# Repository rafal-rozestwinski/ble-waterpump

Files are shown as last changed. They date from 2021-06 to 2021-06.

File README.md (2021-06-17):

# Bluetooth Low Energy IoT Water Pump powered by AA batteries

Another item in my home IoT system, a AA-battery powered pump for watering plants controlled over Bluetooth Low Energy (BLE).

# Design - cheap, fast, reliable vs quick 'n dirty

- Chip nrf51822 is **old and obsolete**, included firmware **(softdevice) is buggy**. But it's **cheap ($1)** and **available** in bulk. When using nrf52* series, I recommend using either native nordic semi SDK or [mbed examples](https://github.com/ARMmbed/mbed-os-example-ble).
- It's an **amazing device for radio controlled battery operated IoT devices**. In this project, it's directly **powered from a two AA batteries**, with **power consumption of around 1.5mA**. Therefore it should work for more than **2 months on a single charge**.
- Three AA batteries power the 5V cheap ($1) watertight water pump. A separate power source for pump here is being used to simplify project and avoid inefficient regulators. Pump, when running, is consuming between 70 and 100mA. [NPM BC547](https://www.mouser.com/datasheet/2/149/BC547-190204.pdf) is rated for 100mA continuous.
- uC battery level is measured and available over BLE GATT service. I changed that to use internal reference voltage, not implemented in mBed.
- **3xAA battery level is not measured**. I check those from time to time, as pump runs for just a few seconds every day.
- Project is downloaded from ARM mbed online IDE and adjust to **work in an offline mode**, using normal GCC ARM build on ubuntu etc.
- No encryption nor secure pairing.
- *WDT is enabled*, but in addition device reboots every 1024 seconds, as a additional failsafe for unstable (old) SoftDevice.
- Just a *few passive components* and a *single [BJT NPM](https://www.mouser.com/datasheet/2/149/BC547-190204.pdf)* transistor being used.
- Code is forked from some mbed example in a quite dirty way. **No warranty** ;)

# Building

- Install ARM GCC on ubuntu: `sudo apt install gcc-arm-none-eabi gdb valgrind make openocd srecord`
- Connect STLINK programmer to SWDIO/SWCLK/GND/VCC pins (with batteries disconnected) and attach to the computer.
- `make && ./RR_FLASH.sh`
- Check using `gatttool` on linux/RPI or via official [nRF Connect app](https://apps.apple.com/app/nrf-connect-for-mobile/id1054362403), which is very useful for debugging BLE in general. 
- Use my python tool `pumpble.py`, available in this directory (including `requirements.txt`).

# Electronic Connection Diagram

As my cheap imported [nrf51822](https://www.nordicsemi.com/Products/Low-power-short-range-wireless/nRF51822) [cheap module](https://botland.com.pl/moduly-bluetooth/4505-modul-bluetooth-low-energy-ble-40-nrf51822-waveshare-9515.html) has 2.0mm goldpin spacing, I'm using [wire-wrapping](https://en.wikipedia.org/wiki/Wire_wrap) technique to connect it.

```
[ 3xAA battery + ] ---------+------[+ 5V water pump -]-----+--------+
                            |                              |        |
                            +------[   |< diode   ]--------+        |  
                                                                 | /
                                          +--[  360 Ohm  ]-----  |   NPN BJT BC547
                                          |                      | \>
                                          |                         |
                                        PIN19                       |
                               ==========================           |
                               |                        |           |
                               |   nrf51822 module      |+-------- Common GND
                     +--VCC +--|                        |           |
                     |         ===========================          |
                     |                       PIN2                   |
                     |                        |                     |
                     |                        |                     |
[ 2*AA battery + ] --+---- [  6800 Ohm  ] ----+---- [ 680 Ohm ] ----+
```

Note: PIN18 is a blinking status LED. Not attached to save battery.

# Hardware

STL and FreeCAD files for attaching pump to the 5mm silicone tube, as well as compatible splitter (so single pump can serve multiple pots etc.). Those are in CAD/ directory.

# Usage [Linux/raspberry pi]

### Find device MAC:

Run `hcitool lescan` and lookup for a device name configured in `main.cpp` as `DEVICE_NAME[]`.

```bash
$ sudo hcitool lescan | grep -i waterpump
C8:5E:22:9A:21:3A waterpump
```

### Find handle values:

```bash
$ gatttool -t random -b C8:5E:22:9A:21:3A --characteristics
(...)
handle = 0x000d, char properties = 0x12, char value handle = 0x000e, uuid = 0000a301-0000-1000-8000-00805f9b34fb
handle = 0x0011, char properties = 0x0a, char value handle = 0x0012, uuid = 0000a101-0000-1000-8000-00805f9b34fb
handle = 0x0014, char properties = 0x02, char value handle = 0x0015, uuid = 0000a201-0000-1000-8000-00805f9b34fb
```

Where first part of UUIDs define services:

- 0000a101-0000-1000-8000-00805f9b34fb -> 0xA101 - pump characteristic uuid for reading and writing a value
- 0000a201-0000-1000-8000-00805f9b34fb -> 0xA201 - uptime characteristic uuid for reading a value
- 0000a301-0000-1000-8000-00805f9b34fb -> 0xA301 - battery characteristic for reading a value

Use `char value handle` value when calling commands below for particular service.

### Read battery state

Value returned is hex-encoded byte, where for example value of 64 => 0x64 => 100 => 100%

`gatttool -t random  -b $MAC --char-read --handle=0x0e | cut -d':' -f2`

### Read uptime

Returns 4 bytes, uint32_t of uptime in seconds since last reboot:

`gatttool -t random  -b $MAC --char-read --handle=0x15 | cut -d':' -f2`

### Read pump state (pumping or not)

`gatttool -t random  -b $MAC --char-read --handle=0x12 | cut -d':' -f2`

### Start pump

Value = seconds for which it should be running, as an hex-encoded byte (and padded with 0!):

`gatttool -t random  -b $MAC --char-write-req -a 0x0012 -n 05`

### Wrapper tool

`LINUX_BLE_GATTTOOL_TEST.sh` is my wrapper to perform those steps. I run it over ssh over my all raspberry pi's all over my home, which is integrated with custom `sensors-dashboard` as well as with the (http://homebridge.io)[HomeBridge] for iOS/HomeKit integration. One can also use iOS Shortcuts app to perform the same.

# Media

Note: always use properly matched batteries ;)

Note: due to a lot of hot glue being used, my implementation has scored only 6/10 repairability score ;)

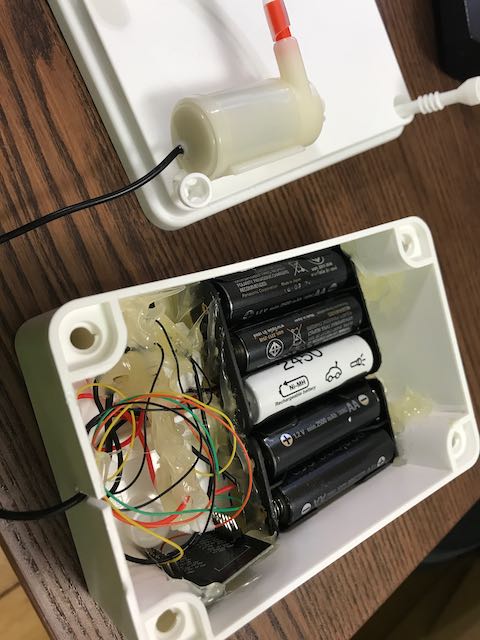
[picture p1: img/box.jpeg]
Photo - inside the box Battery box

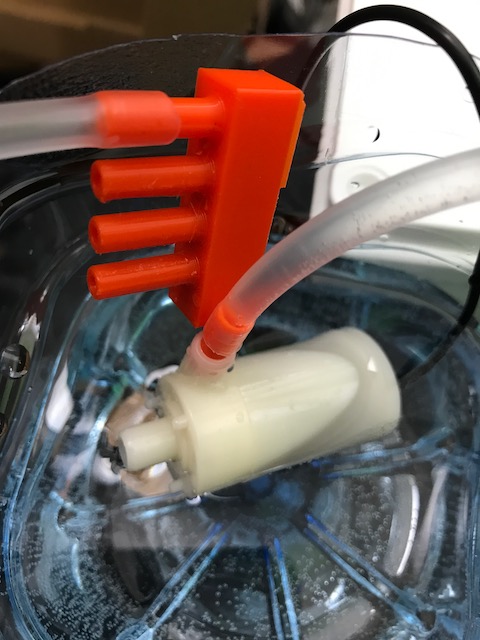
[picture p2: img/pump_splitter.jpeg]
Photo - physical water splitter 3D printed water splitter

Video - pumping water Pumping in action
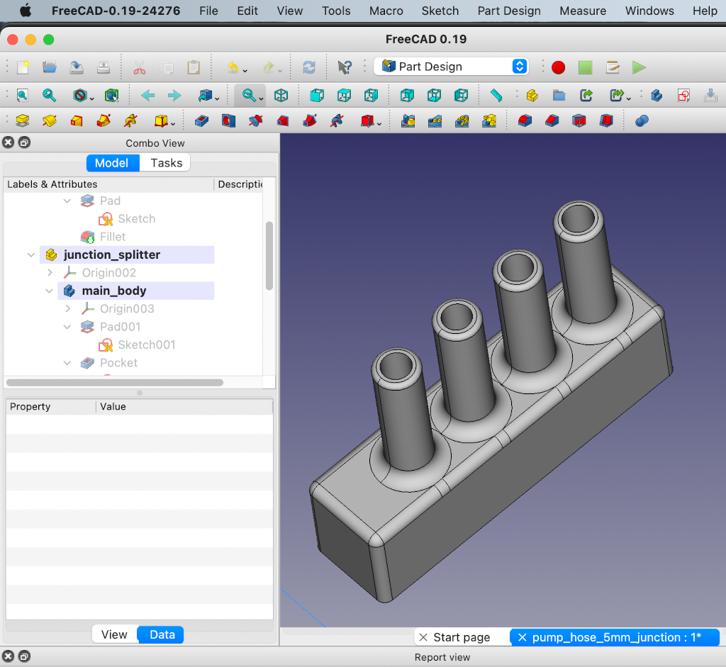
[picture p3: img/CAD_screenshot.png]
FreeCAD - water splitter FreeCAD screenshot of water splitter


# Learn more about GATT and BLE

- https://epxx.co/artigos/bluetooth_gatt.html

# Licensing

All-but-some files in this repo were exported/downloaded from [ARM's mBed Studio online](https://os.mbed.com/studio/).

My changes? Choose: Apache 2, MIT, BSD.

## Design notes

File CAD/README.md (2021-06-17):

# CAD files - STL and FreeCAD

Photo - physical water splitter 3D printed water splitter
FreeCAD - water splitter FreeCAD screenshot of water splitter

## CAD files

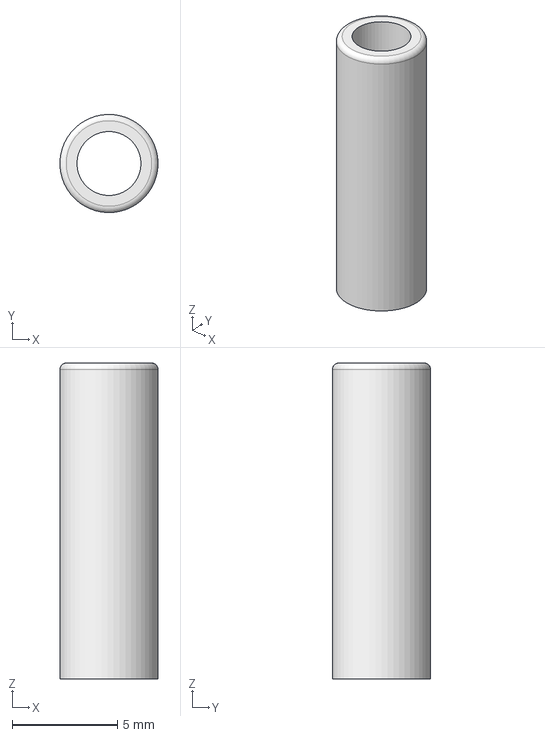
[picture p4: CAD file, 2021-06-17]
CAD/pump_hose_5mm_adapter.FCStd
4.66 x 4.66 x 15.0 mm

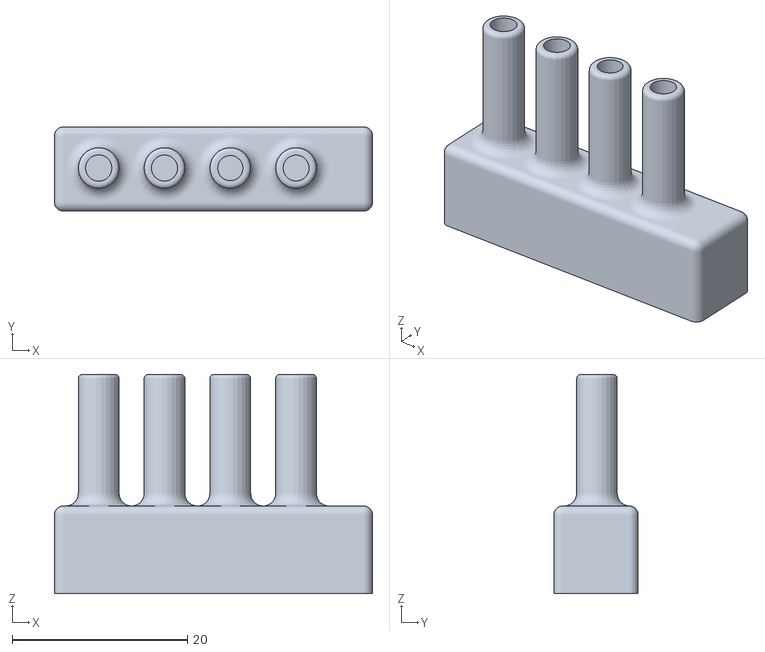
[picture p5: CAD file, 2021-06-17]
CAD/pump_hose_5mm_junction-junction_splitter.stl
36.2 x 9.60 x 25.0

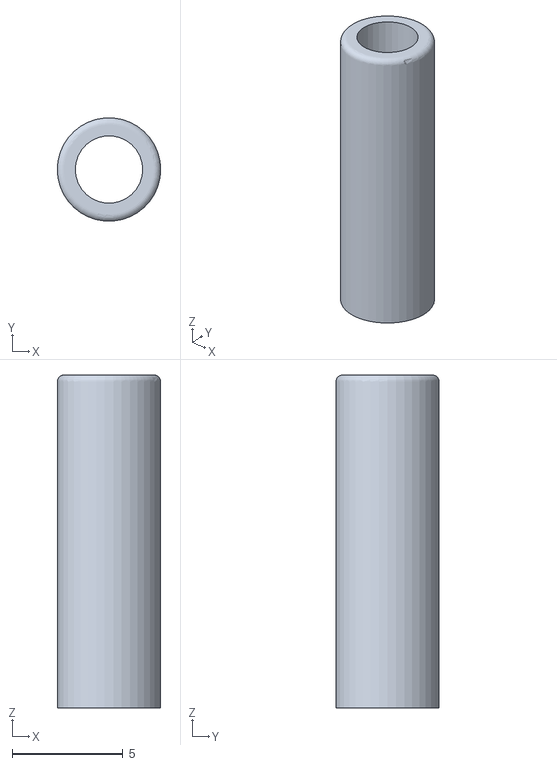
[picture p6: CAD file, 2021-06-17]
CAD/pump_hose_5mm_adapter-Body.stl
4.66 x 4.64 x 15.0

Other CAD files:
CAD/pump_hose_5mm_junction.FCStd

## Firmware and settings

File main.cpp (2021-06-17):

// nrf51822 BLE water pump powered by AA batteries
// by Rafal Rozestwinski
// Modified nrf mbed example.
// My changes under any of: Apache 2.0, BSD, MIT.

#ifndef DEV_NAME
#define DEV_NAME waterpump
#endif

#ifndef DISCONNECT_AFTER_SECONDS
#define DISCONNECT_AFTER_SECONDS 10
#endif

#ifndef RESET_AFTER_SECONDS
#define RESET_AFTER_SECONDS 3600
#endif



#define STRINGIZE(x) #x
#define STRINGIZE_VALUE_OF(x) STRINGIZE(x)

// BATTERY LEVEL:  VCC - R1 - ADC - R2 - GND
// with those values (6.8k + 680R): 12V = 1.09V; 3V = 0.273V; 5V = 0.455
// around 9% of actual value.
#define R1 6800
#define R2 680
#define REFERENCE_VOLTAGE 1.2f

#include <inttypes.h>
#include "ble/BLE.h"
#include "mbed.h"
#include "ble/services/BatteryService.h"
#include "ble/services/DeviceInformationService.h"
#include "nrf.h" // watchdog
#include "cmsis.h"
#include "pinmap.h"

// via ./mbed/TARGET_NRF51822/TOOLCHAIN_GCC_ARM/PinNames.h
//    LED1    = p18,
//    LED2    = p19,
//    LED3    = p20,
//    LED4    = p19,
//    BUTTON1 = p16,
//    BUTTON2 = p17,
//    //  RX_PIN_NUMBER = p11,  TX_PIN_NUMBER = p9,
//    USBTX = TX_PIN_NUMBER,
//    USBRX = RX_PIN_NUMBER,
// DEFAULT: sudo miniterm /dev/ttyUSB0 9600
// HERE: sudo miniterm /dev/ttyUSB0 115200
// Battery voltage with R1 and R2: p2

#define RR_ANALOGIN_MEDIAN_FILTER      1
#define RR_ADC_10BIT_RANGE             0x3FF
#define RR_ADC_RANGE    RR_ADC_10BIT_RANGE

void p2_adc_configure_internal_1_2V_ref() {
    NRF_ADC->ENABLE = ADC_ENABLE_ENABLE_Enabled;
    NRF_ADC->CONFIG = (ADC_CONFIG_RES_10bit << ADC_CONFIG_RES_Pos) |
//                      (ADC_CONFIG_INPSEL_AnalogInputOneThirdPrescaling << ADC_CONFIG_INPSEL_Pos) |
//                      (ADC_CONFIG_REFSEL_VBG << ADC_CONFIG_REFSEL_Pos) |
//                      (ADC_CONFIG_REFSEL_SupplyOneThirdPrescaling << ADC_CONFIG_REFSEL_Pos) | // NRF_ADC_CONFIG_REF_VBG
                      (ADC_CONFIG_PSEL_AnalogInput3 << ADC_CONFIG_PSEL_Pos);// |
//                      (ADC_CONFIG_EXTREFSEL_None << ADC_CONFIG_EXTREFSEL_Pos);
}

uint16_t p2_adc_read_u16() {
    NRF_ADC->CONFIG     &= ~ADC_CONFIG_PSEL_Msk;
    NRF_ADC->CONFIG     |= ADC_CONFIG_PSEL_AnalogInput3 << ADC_CONFIG_PSEL_Pos;
    NRF_ADC->TASKS_START = 1;
    while (((NRF_ADC->BUSY & ADC_BUSY_BUSY_Msk) >> ADC_BUSY_BUSY_Pos) == ADC_BUSY_BUSY_Busy) {
    }
    return (uint16_t)NRF_ADC->RESULT; // 10 bit
}

float p2_adc_read() {
    uint16_t value = p2_adc_read_u16();
    return (float)value * (1.0f / (float)RR_ADC_RANGE);
}

void wdt_init() {
    NRF_WDT->CONFIG = (WDT_CONFIG_HALT_Pause << WDT_CONFIG_HALT_Pos) | ( WDT_CONFIG_SLEEP_Run << WDT_CONFIG_SLEEP_Pos);
    NRF_WDT->CRV = 3*32768;
    NRF_WDT->RREN |= WDT_RREN_RR0_Msk;
    NRF_WDT->TASKS_START = 1;
}

void wdt_reset() {
    NRF_WDT->RR[0] = WDT_RR_RR_Reload;
}

DigitalOut led1(LED1);
DigitalOut powerswitch1(LED2);

Serial serial(USBTX, USBRX, 115200);
Ticker ticker;
volatile uint32_t cnt = 0;

void rr_reset() {
    NVIC_SystemReset();
}

void periodicCallback(void);
const char* get_current_sensor_name(int b1, int b2);

void rr_error() {
    serial.printf("> rr_error() - 1s loop for debugger now!\n");
    ticker.detach();
    ticker.attach(periodicCallback, 0.1);
    wait_ms(1000);
    rr_reset();
}

float nrf51_voltage_adc_to_battery(float adc_in) {
    float real_voltage_on_pin = adc_in * REFERENCE_VOLTAGE;
    //int R1 = 21000; // defined as macro
    //int R2 = 1000; //  defined as macro
    //   Vs ----- R1 ------ Vout_PIN ---- R2 ----- GND
    //
    //         Vs * R2
    // Vout = ---------------
    //        ( R1 + R2)
    //
    //          Vout
    // Vs =   -------- * ( R1 + R2)
    //          R2
    float actualVoltage = (real_voltage_on_pin / R2) * (R1 + R2);
    return actualVoltage;
}

int32_t map(int32_t x, int32_t in_min, int32_t in_max, int32_t out_min, int32_t out_max) {
    int32_t ret = (x - in_min) * (out_max - out_min) / (in_max - in_min) + out_min;
    if(ret > out_max) return out_max;
    if(ret < out_min) return out_min;
    return ret;
}

float LAST_BATTERY_VOLTAGE = 0.0f;
uint8_t LAST_BATTERY_PERCENT = 0;

float get_current_battery_voltage() {
    float adc_out = p2_adc_read(); // using internal 1.2V reference voltage, same below.
    float voltage = nrf51_voltage_adc_to_battery(adc_out);
    return voltage;
}

void periodicCallback(void) {
    led1 = !led1;
    cnt++;
}

class WaterPumpService {
public:
    const static uint16_t WATER_PUMP_SERVICE_UUID              = 0xA100;
    const static uint16_t WATER_PUMP_STATE_CHARACTERISTIC_UUID = 0xA101;

    WaterPumpService(BLEDevice &_ble, uint8_t initial) :
        ble(_ble), pumpingValue(initial), pumpState(WATER_PUMP_STATE_CHARACTERISTIC_UUID, &initial) {
        GattCharacteristic *charTable[] = {&pumpState};
        GattService pumpService(WATER_PUMP_SERVICE_UUID, charTable, sizeof(charTable) / sizeof(GattCharacteristic *));
        ble.addService(pumpService);
    }

    GattAttribute::Handle_t getValueHandle() const {
        return pumpState.getValueHandle();
    }

    void updatePumpState(uint8_t v) {
        pumpingValue = v;
        ble.gattServer().write(pumpState.getValueHandle(), &pumpingValue, 1);
    }

private:
    BLEDevice &ble;
    uint8_t pumpingValue;
    ReadWriteGattCharacteristic<uint8_t> pumpState;
};

class CustomBatteryService {
public:
    const static uint16_t CUSTOM_BATTERY_SERVICE_UUID              = 0xA300;
    const static uint16_t CUSTOM_BATTERY_CHARACTERISTIC_UUID = 0xA301;

    CustomBatteryService(BLE &_ble, uint8_t level = 100) :
        ble(_ble),
        batteryLevel(level),
        batteryLevelCharacteristic(CUSTOM_BATTERY_CHARACTERISTIC_UUID, &batteryLevel, GattCharacteristic::BLE_GATT_CHAR_PROPERTIES_NOTIFY) {

        GattCharacteristic *charTable[] = {&batteryLevelCharacteristic};
        GattService         batteryService(CUSTOM_BATTERY_SERVICE_UUID, charTable, sizeof(charTable) / sizeof(GattCharacteristic *));

        ble.addService(batteryService);
    }
    void updateBatteryLevel(uint8_t newLevel) {
        batteryLevel = newLevel;
        ble.gattServer().write(batteryLevelCharacteristic.getValueHandle(), &batteryLevel, 1);
    }

protected:
    BLE &ble;
    uint8_t    batteryLevel;
    ReadOnlyGattCharacteristic<uint8_t> batteryLevelCharacteristic;
};

class UptimeService {
public:
    const static uint16_t UPTIME_SERVICE_UUID              = 0xA200;
    const static uint16_t UPTIME_STATE_CHARACTERISTIC_UUID = 0xA201;

    UptimeService(BLEDevice &_ble, uint32_t initial) :
        ble(_ble), value(initial), valueState(UPTIME_STATE_CHARACTERISTIC_UUID, &initial) {
        GattCharacteristic *charTable[] = {&valueState};
        GattService         uptimeService(UPTIME_SERVICE_UUID, charTable, sizeof(charTable) / sizeof(GattCharacteristic *));
        ble.addService(uptimeService);
    }

    GattAttribute::Handle_t getValueHandle() const {
        return valueState.getValueHandle();
    }

    void updateUptimeState(uint32_t v) {
        value = v;
        ble.gattServer().write(valueState.getValueHandle(), (uint8_t*)&value, 4);
    }

private:
    BLEDevice &ble;
    uint32_t value;
    ReadOnlyGattCharacteristic<uint32_t> valueState;
};

const static char DEVICE_NAME[] = STRINGIZE_VALUE_OF(DEV_NAME);
static const uint16_t uuid16_list[] = {
    WaterPumpService::WATER_PUMP_SERVICE_UUID,
    UptimeService::UPTIME_SERVICE_UUID,
    GattService::UUID_BATTERY_SERVICE,
    GattService::UUID_DEVICE_INFORMATION_SERVICE,
    CustomBatteryService::CUSTOM_BATTERY_SERVICE_UUID
};

WaterPumpService *pumpServicePtr = NULL;
UptimeService *uptimeServicePtr = NULL;
CustomBatteryService *batteryServicePtr = NULL;
DeviceInformationService *deviceInfo = NULL;

volatile uint32_t PUMPING_STOP_AT_CNT = 0;
volatile bool PUMPING_ENABLED = false;

void onDataWrittenCallback(const GattWriteCallbackParams *params) {
    if ((params->handle == pumpServicePtr->getValueHandle()) && (params->len == 1)) {
        int pump_for_seconds = (int)(*(params->data));
        serial.printf("PUMP DATA: %i\n", pump_for_seconds);
        PUMPING_STOP_AT_CNT = cnt + pump_for_seconds + 1;
        PUMPING_ENABLED = true;
        powerswitch1 = 1;
        if(pumpServicePtr) {
            pumpServicePtr->updatePumpState(pump_for_seconds);
            serial.printf("!!    -> pumpServicePtr updated to value %i\n", (int)pump_for_seconds);
        } else {
            serial.printf("WARNING: pumpServicePtr is NULL!\n");
            rr_error();
        }
        return;
    }
}

void onBleInitError(BLE& ble, ble_error_t error) {
    rr_error();
}

void disconnectionCallback(const Gap::DisconnectionCallbackParams_t* params) {
    serial.printf("\n\n\nDisconnected!\n\n\n");
    BLE::Instance().gap().startAdvertising();
}

uint32_t CONNECTED_AT = 0;
uint32_t DISCONNECT_AT = 999999;

void connectionCallback(const Gap::ConnectionCallbackParams_t *params) {
    CONNECTED_AT = cnt;
    DISCONNECT_AT = cnt + DISCONNECT_AFTER_SECONDS;
    serial.printf("\n\n\nConnected! will disconnect at: %u \n\n\n", (unsigned int)DISCONNECT_AT);
}

void bleInitComplete(BLE::InitializationCompleteCallbackContext *params) {
    BLE& ble = params->ble;
    ble_error_t error = params->error;
    if (error != BLE_ERROR_NONE) {
        onBleInitError(ble, error);
        return;
    }
    if(ble.getInstanceID() != BLE::DEFAULT_INSTANCE) {
        return;
    }
    ble.gap().onDisconnection(disconnectionCallback);
    ble.gap().onConnection(connectionCallback);
    ble.gattServer().onDataWritten(onDataWrittenCallback);

    batteryServicePtr = new CustomBatteryService(ble, LAST_BATTERY_PERCENT);
    pumpServicePtr = new WaterPumpService(ble, (uint8_t)0);
    uptimeServicePtr = new UptimeService(ble, (uint32_t)0);
    deviceInfo = new DeviceInformationService(ble, "(c)RR", "ble-waterpump", "SN0001", "hw-rev1", "fw-rev1", "soft-rev3");

    ble.gap().accumulateAdvertisingPayload(GapAdvertisingData::BREDR_NOT_SUPPORTED | GapAdvertisingData::LE_GENERAL_DISCOVERABLE);
    ble.gap().accumulateAdvertisingPayload(GapAdvertisingData::COMPLETE_LIST_16BIT_SERVICE_IDS, (uint8_t *)uuid16_list, sizeof(uuid16_list));
    ble.gap().accumulateAdvertisingPayload(GapAdvertisingData::COMPLETE_LOCAL_NAME, (uint8_t *)DEVICE_NAME, sizeof(DEVICE_NAME));
    ble.gap().setAdvertisingType(GapAdvertisingParams::ADV_CONNECTABLE_UNDIRECTED);
    ble.gap().setAdvertisingInterval(1000);
    ble.gap().startAdvertising();
}

int main() {
    wdt_init();
    wait_ms(1000);
    wdt_reset();
    led1 = 1;
    powerswitch1 = 0;
    cnt = 0;
    serial.printf("! Starting board, device name is '%s'\n", STRINGIZE_VALUE_OF(DEV_NAME));
    p2_adc_configure_internal_1_2V_ref();
    ticker.attach(periodicCallback, 1);
    BLE &ble = BLE::Instance();
    serial.printf("! BLE init...\n");
    ble.init(bleInitComplete);
    serial.printf("! BLE init complete!\n");
    while (ble.hasInitialized() == false) { } // spinlock
    uint32_t prev_cnt = 0;
    wdt_reset();
    while (true) {
        if(cnt > RESET_AFTER_SECONDS) {
            serial.printf("\n\n\n!!!!!cnt > %u, soft reset to keep things running...\n\n\n", RESET_AFTER_SECONDS);
            rr_reset();
            serial.printf("\n\n\n this msg should not appear!\n\n\n\n");
        }
	if(cnt >= DISCONNECT_AT) {
		serial.printf("Forcing client disconnection (disconnect_at=%u)\n\n\n", (unsigned int)DISCONNECT_AT);
		ble.disconnect(Gap::CONNECTION_TIMEOUT);
		DISCONNECT_AT = 999999;
	}
        if(cnt != prev_cnt) {
            prev_cnt = cnt;
            serial.printf("cnt=%u ", (unsigned)cnt);
            if(uptimeServicePtr) {
                uptimeServicePtr->updateUptimeState(cnt);
            }
            wdt_reset();
            if(PUMPING_ENABLED) {
                serial.printf("\n\n! pumping cnt=%u till=%u\n", (unsigned int)cnt, (unsigned int)PUMPING_STOP_AT_CNT);
                if(cnt >= PUMPING_STOP_AT_CNT) {
                    serial.printf("\n\n! STOPPING PUMP!\n\n");
                    powerswitch1 = 0;
                    PUMPING_ENABLED = false;
                    PUMPING_STOP_AT_CNT = 0;
                    if(pumpServicePtr) {
                        pumpServicePtr->updatePumpState(0);
                        serial.printf("!!    -> pumpServicePtr updated to value 0\n");
                    } else {
                        serial.printf("WARNING: pumpServicePtr is NULL!\n");
                        rr_error();
                    }
                }
                //if(pumpServicePtr) {
                //	pumpServicePtr->updatePumpState(PUMPING_STOP_AT_CNT - cnt);
                //	//serial.printf("!!    -> pumpServicePtr updated to value %i\n", (int)(PUMPING_STOP_AT_CNT - cnt));
                //} else {
                //	serial.printf("WARNING: pumpServicePtr is NULL!\n");
                //}
            }

            LAST_BATTERY_VOLTAGE = get_current_battery_voltage();
            LAST_BATTERY_PERCENT = map((int)(LAST_BATTERY_VOLTAGE * 1000), 1800, 3200, 0, 100);
            //serial.printf("# update svc data cnt=%u battery= (int)%i[mV] (est_battery_percent=%i)\n", (unsigned int)cnt, (int)LAST_BATTERY_VOLTAGE*1000, (int)LAST_BATTERY_PERCENT);
            if(batteryServicePtr) {
                batteryServicePtr->updateBatteryLevel(LAST_BATTERY_PERCENT);
                //serial.printf("BatteryService - level updated\n");
            } else {
                serial.printf("BatteryServicePtr is NULL!\n");
                rr_error();
            }

        }
        ble.waitForEvent();
    }
}
